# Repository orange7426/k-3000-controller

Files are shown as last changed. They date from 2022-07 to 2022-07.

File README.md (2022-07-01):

# k-3000-controller
Smart controller for K-3000 hand blender.

## Features

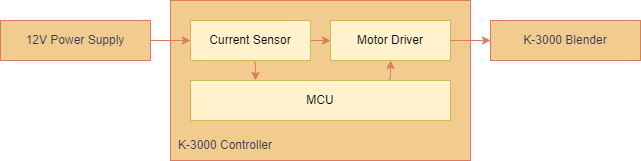
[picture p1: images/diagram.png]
Diagram


- **Non-instrusive**: The controller is a non-intrusive device. It controls the blender with original power inputs.
- **Control over internet**: Both WiFi and Bluetooth are supported. The project provides a default wifi interface. By proper proxy setting, it can be controlled from anywhere in the world.
- **Count each stroke**: The device "knows" the stroke being executed by measuing the motor current. It empowers user to add any arbitrary delay between strokes.

## Images

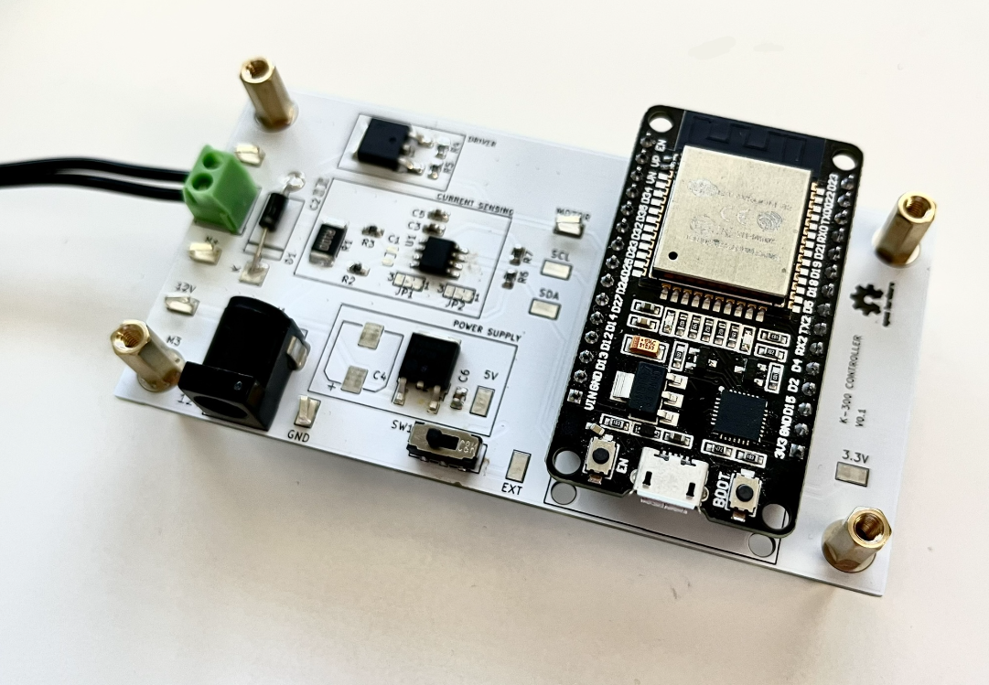
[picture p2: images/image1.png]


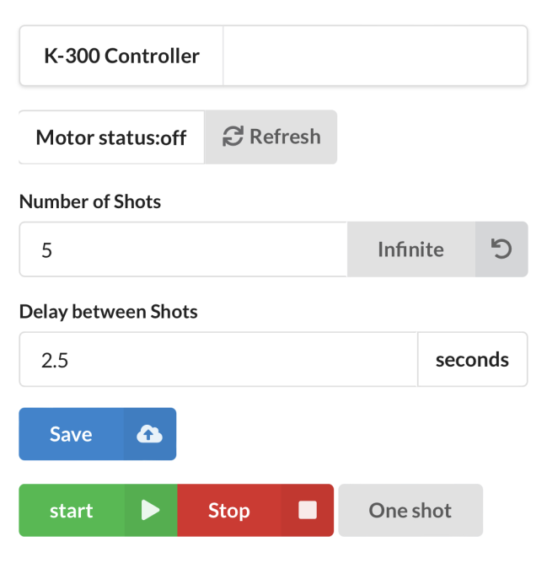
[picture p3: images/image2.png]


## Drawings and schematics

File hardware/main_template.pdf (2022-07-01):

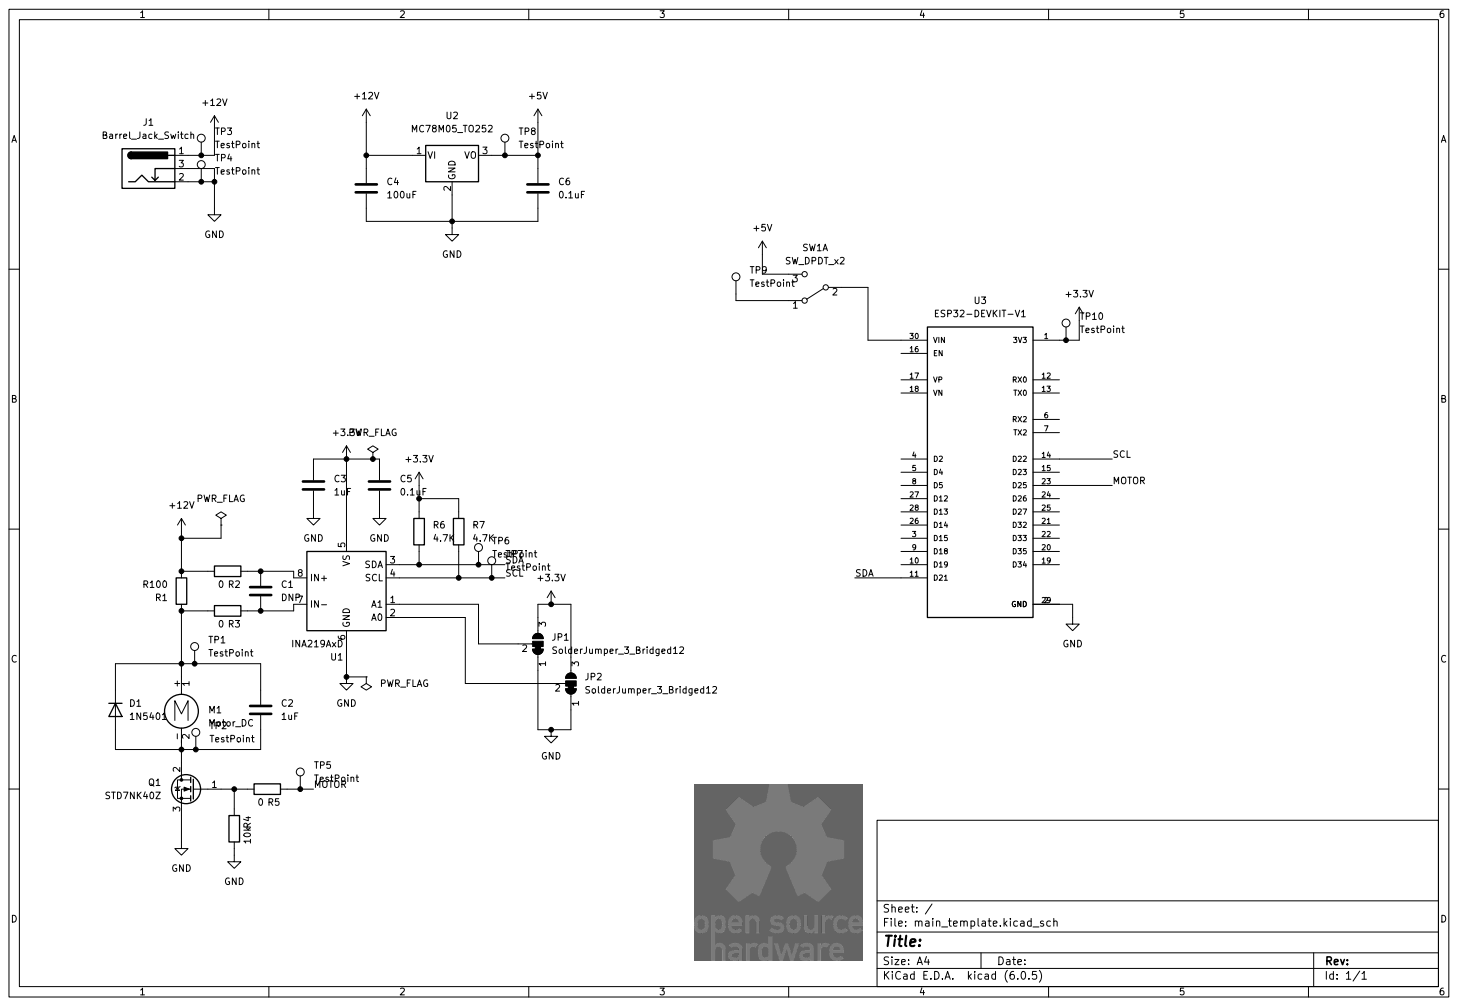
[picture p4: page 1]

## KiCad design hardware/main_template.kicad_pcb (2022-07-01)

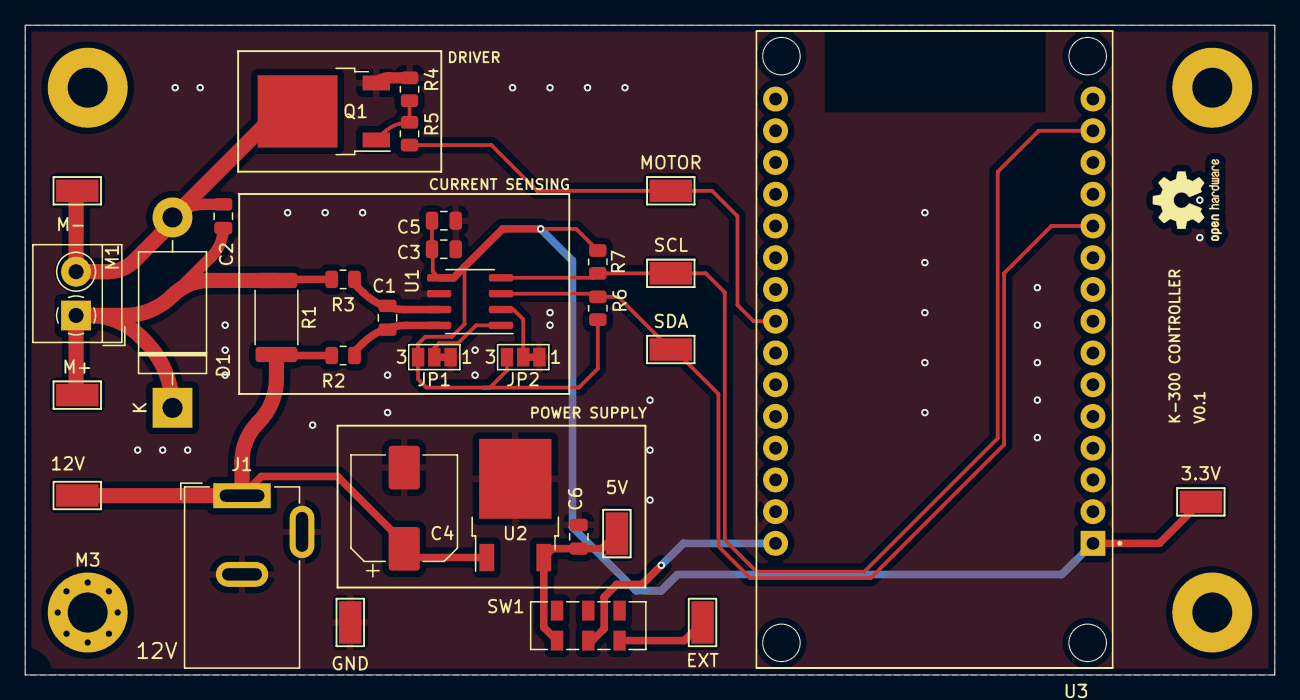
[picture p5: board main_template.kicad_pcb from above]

Board: 4 copper layers, 100.0 x 52.0 mm, 34 parts (0 on the bottom side), 16 nets.

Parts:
3.3V, 5V, 12V: TestPoint; TestPoint_Keystone_5015_Micro-Minature
C1: DNP; C_0805_2012Metric
C2, C3: 1uF; C_0805_2012Metric
C4: 100uF; CP_Elec_8x10
C5, C6: 0.1uF; C_0805_2012Metric
D1: 1N5401; D_DO-201AD_P15.24mm_Horizontal
EXT: TestPoint; TestPoint_Keystone_5015_Micro-Minature
GND: TestPoint; TestPoint_Keystone_5015_Micro-Minature
J1: Barrel_Jack_Switch; BarrelJack_GCT_DCJ200-10-A_Horizontal
JP1, JP2: SolderJumper_3_Bridged12; SolderJumper-3_P1.3mm_Bridged12_Pad1.0x1.5mm_NumberLabels
M1: Motor_DC; TerminalBlock_4Ucon_1x02_P3.50mm_Horizontal
M3: MountingHole_3.2mm_M3_Pad_Via
M+: TestPoint; TestPoint_Keystone_5015_Micro-Minature
M-: TestPoint; TestPoint_Keystone_5015_Micro-Minature
MOTOR: TestPoint; TestPoint_Keystone_5015_Micro-Minature
Q1: STD7NK40Z; TO-252-2
R1: R100; R_2512_6332Metric
R2, R3, R5: 0; R_0805_2012Metric
R4: 10k; R_0805_2012Metric
R6, R7: 4.7K; R_0805_2012Metric
SCL: TestPoint; TestPoint_Keystone_5015_Micro-Minature
SDA: TestPoint; TestPoint_Keystone_5015_Micro-Minature
SW1: SW_DPDT_x2; SW_DPDT_CK_JS202011JCQN
U1: INA219AxD; SOIC-8_3.9x4.9mm_P1.27mm
U2: MC78M05_TO252; TO-252-2
U3: ESP32-DEVKIT-V1; MODULE_ESP32_DEVKIT_V1

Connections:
+3V3: 3.3V.1, C3.2, C5.2, JP1.3 (B), JP2.3 (B), R6.1, R7.1, U1.5 (VS), U3.1 (3V3)
+5V: 5V.1, C6.1, SW1.3 (C), U2.3 (VO)
+12V: 12V.1, C4.1, J1.1, R1.2, R2.2, U2.1 (VI)
/MOTOR: MOTOR.1, R5.1, U3.23 (D25)
/SCL: R7.2, SCL.1, U1.4 (SCL), U3.14 (D22)
/SDA: R6.2, SDA.1, U1.3 (SDA), U3.11 (D21)
GND: C3.1, C4.2, C5.1, C6.2, GND.1, J1.2, J1.3, JP1.1 (A), JP2.1 (A), Q1.3 (S), R4.2, U1.6 (GND), U2.2 (GND), U3.2 (GND), U3.29 (GND)
unnamed: C1.1, R3.1, U1.7 (IN-)
unnamed: C1.2, R2.1, U1.8 (IN+)
unnamed: C2.1, D1.1 (K), M1.1 (+), M+.1, R1.1, R3.2
unnamed: C2.2, D1.2 (A), M1.2 (-), M-.1, Q1.2 (D)
unnamed: JP1.2 (C), U1.1 (A1)
unnamed: JP2.2 (C), U1.2 (A0)
unnamed: Q1.1 (G), R4.1, R5.2
unnamed: EXT.1, SW1.1 (A)
unnamed: SW1.2 (B), U3.30 (VIN)

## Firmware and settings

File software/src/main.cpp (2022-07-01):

#include "Arduino.h"

#include <Wire.h>
#include <Adafruit_INA219.h>

#include <filters.h>

#include <WiFi.h>
#include <AsyncTCP.h>
#include <ESPAsyncWebServer.h>

#include "SPIFFS.h"

#include <ArduinoJson.h>

// Constants

#define SINGLE_SHOT_TIMEOUT 1500

#define PRE_SHOT_DELAY 100
#define POST_SHOT_DELAY 100

// Status

DynamicJsonDocument status(1024);
bool isMotorEnabled = false;
int numberOfShots = 0;
double delayBetweenShots = 0;

// Motor

#define MOTOR 25

void setMotorEnabled(bool);

// Network

const char* ssid = "***";
const char* password = "***";

AsyncWebServer server(80);
AsyncWebSocket ws("/ws");

void onEvent(AsyncWebSocket *, AsyncWebSocketClient *, AwsEventType, void *, uint8_t *, size_t);

// Current sensing

Adafruit_INA219 ina219;

const float cutoff_freq   = 20.0;
const float sampling_time = 2.0f / 1000.0f;
IIR::ORDER  order = IIR::ORDER::OD2;

// Low-pass filter
Filter f(cutoff_freq, sampling_time, order);

void initFS() {
  if (!SPIFFS.begin()) {
    Serial.println("An error has occurred while mounting SPIFFS");
  }
  else{
   Serial.println("SPIFFS mounted successfully");
  }
}

void initWiFi() {
  WiFi.mode(WIFI_STA);
  WiFi.begin(ssid, password);
  Serial.print("Connecting to WiFi ..");
  while (WiFi.status() != WL_CONNECTED) {
    Serial.print('.');
    delay(1000);
  }
  Serial.println(WiFi.localIP());
}

void initWebSocket() {
  ws.onEvent(onEvent);
  server.addHandler(&ws);
}

void notifyAllClients();

void initIna219() {
  if (!ina219.begin()) {
    Serial.println("Failed to find INA219 chip");
    while (1) { delay(10); }
  }
}

void setup()
{
  Serial.begin(115200);
  while (!Serial) {
      // will pause Zero, Leonardo, etc until serial console opens
      delay(1);
  }

  pinMode(LED_BUILTIN, OUTPUT);
  pinMode(MOTOR, OUTPUT);
  status["isMotorEnabled"] = false;

  initFS();
  initWiFi();
  initWebSocket();
  initIna219();
  
  server.on("/", HTTP_GET, [](AsyncWebServerRequest *request){
    request->send(SPIFFS, "/index.html", "text/html");
  });
  server.serveStatic("/", SPIFFS, "/");

  server.begin();
  Serial.println("HTTP server started");
}

enum State {
  idle,
  start,
  executing,
  releasing,
  cooling,
};

State prevState = idle;
State state = idle;

double currentStateTimer = 0;

uint32_t sampleSize = 0;
double averagePower = 0;

uint32_t timer;

void loop()
{
  double dt = (double)(micros() - timer) / 1000000; // Calculate delta time
  timer = micros();

  if (prevState != state) {
    prevState = state;
    currentStateTimer = 0;
  }
  currentStateTimer += dt;

  if (state == idle) {
    setMotorEnabled(false);
  } else if (state == start) {
    if (numberOfShots == -1 || numberOfShots > 0) {
      if (numberOfShots > 0) numberOfShots --;
      setMotorEnabled(true);
      // Start listening for power peak
      sampleSize = 0;
      averagePower = 0;
      // Pre shot delay to make sure motor is on
      delay(PRE_SHOT_DELAY);
      // Update state to executing
      state = executing;
    } else {
      state = idle;
    }
  } else if (state == executing) {
    // Calculate average power
    float power = f.filterIn(ina219.getPower_mW());
    averagePower = (averagePower * sampleSize + power) / (sampleSize + 1);
    sampleSize += 1;
    // Wait for power peak
    if (power > averagePower * 1.5 || currentStateTimer > SINGLE_SHOT_TIMEOUT) {
      state = releasing;
    }
  } else if (state == releasing) {
    // Calculate average power
    float power = f.filterIn(ina219.getPower_mW());
    averagePower = (averagePower * sampleSize + power) / (sampleSize + 1);
    sampleSize += 1;
    // Wait for power drop
    if (power < averagePower * 1.5 || currentStateTimer > SINGLE_SHOT_TIMEOUT) {
      // Post shot delay to make sure spring is released
      delay(POST_SHOT_DELAY);
      setMotorEnabled(false);

      state = cooling;
    }
  } else if (state == cooling) {
    // Wait for timeout
    if (currentStateTimer > delayBetweenShots) {
      state = start;
      notifyAllClients();
    }
  }

  delay(2);
}

void setMotorEnabled(bool enabled) {
  if (isMotorEnabled == enabled) return;
  isMotorEnabled = enabled;
  digitalWrite(LED_BUILTIN, enabled ? HIGH : LOW);
  digitalWrite(MOTOR, enabled ? HIGH : LOW);
  notifyAllClients();
}

void syncStatus() {
  status["isMotorEnabled"] = isMotorEnabled;
  status["numberOfShots"] = numberOfShots;
  status["delayBetweenShots"] = delayBetweenShots;
}

void notifyAllClients() {
  syncStatus();
  String json = "";
  serializeJson(status, json);
  ws.textAll(json);
}

void onEvent(AsyncWebSocket *server, AsyncWebSocketClient *client, AwsEventType type, void *arg, uint8_t *data, size_t len) {
  switch (type) {
    case WS_EVT_CONNECT:
      Serial.printf("WebSocket client #%u connected from %s\n", client->id(), client->remoteIP().toString().c_str());
      break;
    case WS_EVT_DISCONNECT:
      Serial.printf("WebSocket client #%u disconnected\n", client->id());
      break;
    case WS_EVT_DATA: {
      AwsFrameInfo *info = (AwsFrameInfo*)arg;
      if (info->final && info->index == 0 && info->len == len && info->opcode == WS_TEXT) {
        data[len] = 0;
        String message = (char*)data;
        if (message.indexOf("status") >= 0) {
          syncStatus();
          String json = "";
          serializeJson(status, json);
          client->text(json);
        }
        if (message.indexOf("{") >= 0) {
          DynamicJsonDocument patch(1024);
          deserializeJson(patch, message);
          if (patch.containsKey("numberOfShots")) {
            numberOfShots = patch["numberOfShots"];
          }
          if (patch.containsKey("delayBetweenShots")) {
            delayBetweenShots = patch["delayBetweenShots"];
          }
          if (patch.containsKey("state")) {
            String newState = patch["state"];
            if (newState.equals("start")) {
              state = start;
            } else if (newState.equals("idle")) {
              state = idle;
            }
          }
          notifyAllClients();
        }
        if (message.indexOf("on") >= 0) {
          state = start;
          notifyAllClients();
        }
        if (message.indexOf("off") >= 0) {
          state = idle;
          notifyAllClients();
        }
        if (message.indexOf("os") >= 0) {
          numberOfShots = 1;
          state = start;
          notifyAllClients();
        }
      }
      break;
    }
    case WS_EVT_PONG:
    case WS_EVT_ERROR:
      break;
  }
}

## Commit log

2022-07-01 Add hardware schematic and pcb layout
    [main_template-B_Mask.gbs, main_template-B_Paste.gbp, main_template-B_Silkscreen.gbo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]
2022-07-01 upload gerber zip
